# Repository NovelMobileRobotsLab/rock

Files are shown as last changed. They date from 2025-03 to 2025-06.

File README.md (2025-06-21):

# Rolling One-motor Controlled rocK (ROCK)

<p float="middle">
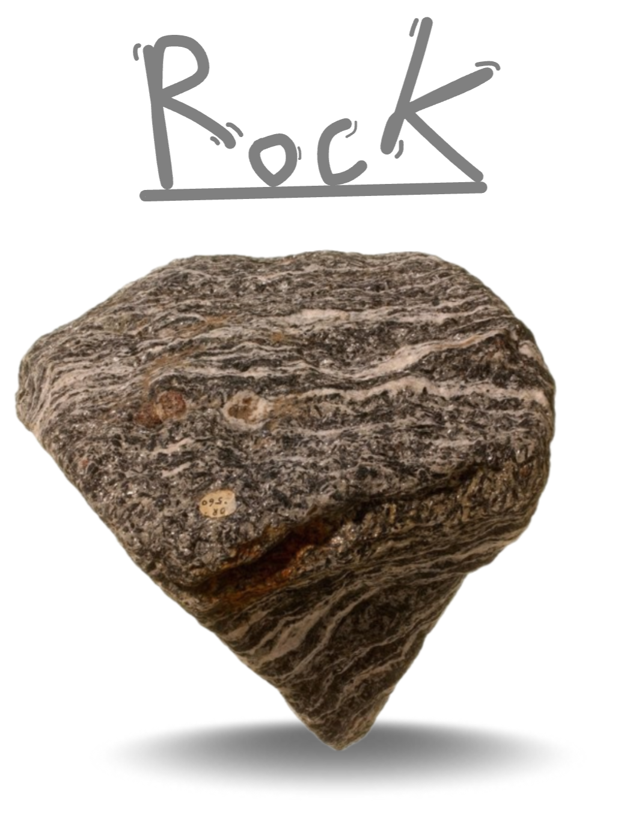
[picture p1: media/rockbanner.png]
  
</p>

A fully enclosed shape that tumbles and jumps; controllable movement on a flat surface with only 1 motor and 2 rigid bodies.

<p float="middle">
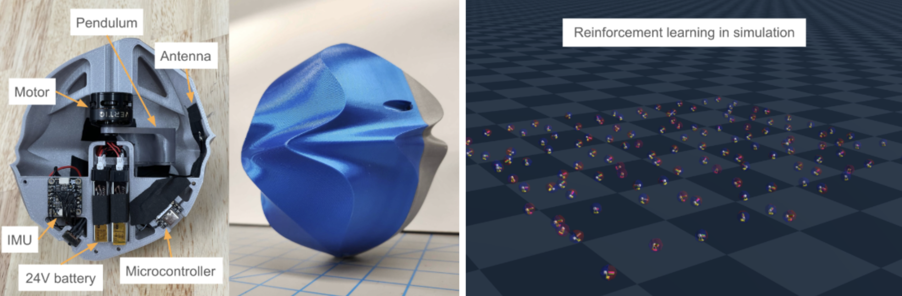
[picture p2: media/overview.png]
  
</p>

<p float="middle">
  
</p>

# Hardware
- Microcontroller: Seeeduino Xiao ESP32S3
- Motor: Vertiq 23-06 G1 220KV brushless motor
- IMU: Adafruit BNO085
- Shell: 3D printed
- Pendulum: 3D printed, filled with lead
- Battery: 6x Tattu 220mAh LiPo (22.2V)

An uneven shell creates steering affordances, using the complex ground contacts to couple the dynamics between motion in multiple dimensions. We iterated over 3 designs to improve continuous rolling, consistent turning, and option for interchangable attachments for diverse maneuvers:
<p float="middle">
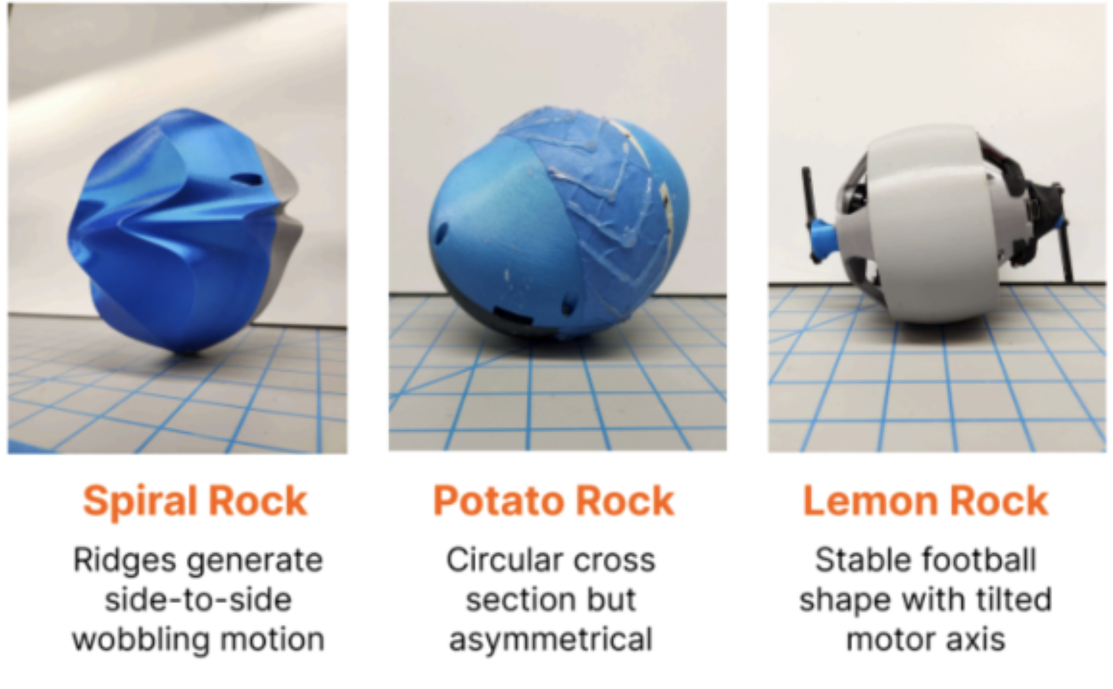
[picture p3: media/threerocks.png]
  
</p>

# Control

<p float="middle">
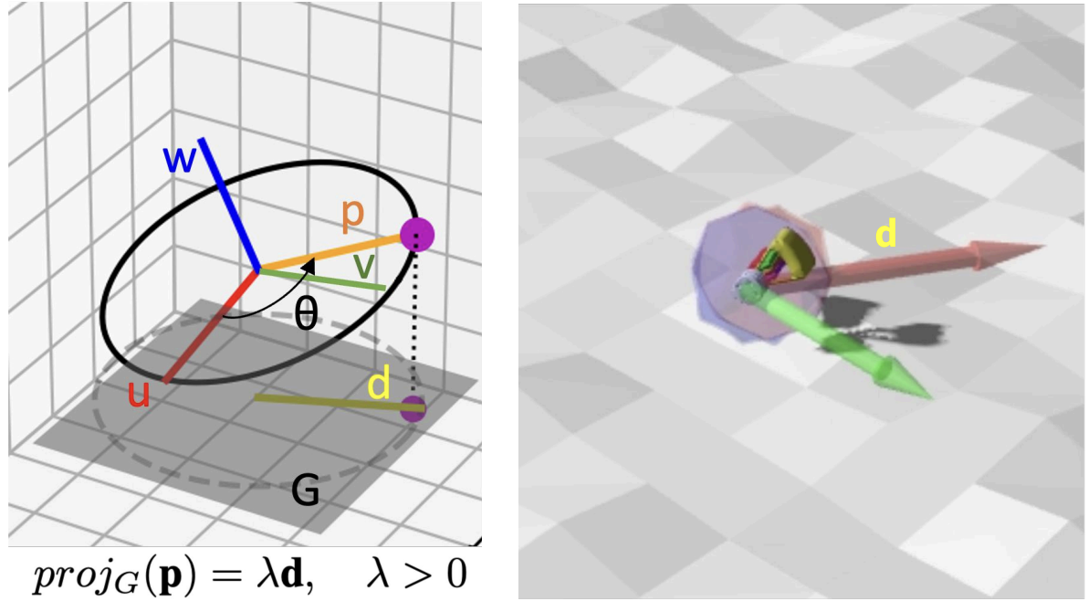
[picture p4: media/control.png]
  
</p>
The robot is teleoperated by commanding a desired rolling direction. We create a simple controller that rolls by offsetting the robot’s center of mass in the direction by manual joystick input.  We also train a reinforcement learning policy to use dynamic pendulum movements for higher performance. The policy is quantized to run on the microcontroller at 90 Hz.

<p float="middle">
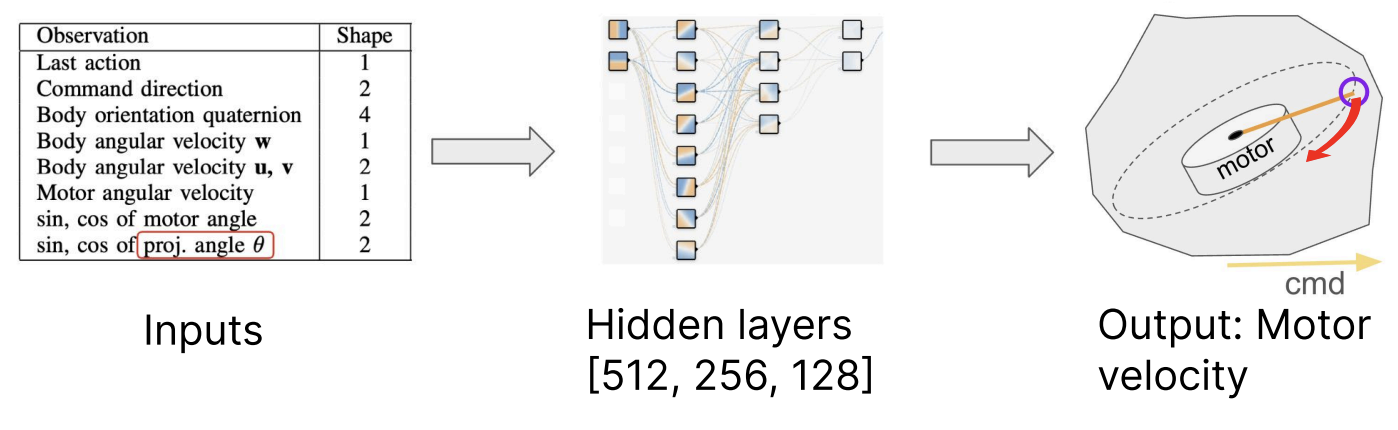
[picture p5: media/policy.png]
  
</p>

# Installation

Create python virtual environment (we use python3.12):
```bash
python3 -m venv .venv
source .venv/bin/activate
```

Install dependencies (genesis-world enforces stricter than necessary version requirements so we install it with --no-deps):
```bash
pip install -r requirements.txt
pip install genesis-world --no-deps
```

# Files directory
```
rock/
├── embedded/
│   ├── convert_torch_to_tflite/     # Convert PyTorch models to TFLite for ESP32
│   ├── esp-tf_speedtest_fw/         # PlatformIO project testing inference speed
│   ├── gimbal_prototype_fw/         # PlatformIO project gimbal prototype
│   └── rock2_fw/                    # PlatformIO project for latest ROCK
│       ├── src/                     # Source code directory
│       │   ├── main.cpp             # Main control loop firmware
│       │   ├── util.h               # Utility functions for IMU and motor control
│       │   ├── all_ops_resolver.h   # TFLite operation definitions
│       │   ├── model_13_26_700.h    # Header for trained model on rough terrain
│       │   ├── model_13_26_700.cpp  # Trained model weights on rough terrain
│       │   ├── model_58_02_200.h    # Header for trained model on smooth terrain
│       │   └── model_58_02_200.cpp  # Trained model weights on smooth terrain
│       ├── trained_models/          # Original TFLite model files
│       └── platformio.ini           # Project configuration and dependencies
├── genesis-sim/
│   ├── balancing/                   # RL environment for balancing, unfinished
│   └── tumbling/                    # RL environment for tumbling, main work
│       ├── rock_env.py              # Defines how the simulation behaves
│       ├── rock_train.py            # Start parallel simulation training
│       ├── rock_eval.py             # Run simulation for policy evaluation 
│       ├── viewer.py                # Run simulation just for viewing
│       ├── analyze_runs.ipynb       # Analyzing run performance with plots
│       ├── runs/                    # Training run output
│       ├── autoruns/                # Automated run output
│       ├── projruns/                # Runs with projection controller
│       └── penaltysweep/            # Runs with sweep of penalty weights
├── onshape/                         # updating cad in python and generating URDF
│   ├── balo/                        # almost symmetric balo shape
│   ├── balo2/                       # test hexagonal shape with stretched vertex
│   ├── intuition2/                  # spiral shell (mostly used this)
│   ├── pmrock/                      # parametric minimal rock
│   ├── rock1/                       # jointed 1 dof rock
│   └── weird_rock/                  # potato shell
├── rockstation/
│   ├── cmdlogs/                     # CSV logs from rockstation
│   ├── decode.ipynb                 # Testing telemetry decoding
│   ├── loganalysis.ipynb            # Notebook for analyzing cmdlogs
|   ├── periodics.py                 # Helper for running functions at fixed rate
│   └── rockstation1-5.py            # Run this to control the robot from laptop
└── sandbox/
    ├── acrobot/                     # Jumping rock is kinda like acrobot
    ├── from_matlab/                 # Prof Yim's MATLAB dynamics, translated
    ├── gpu_accel/                   # Messing around with Taichi and trajopt
    ├── imu_sim/                     # Attempt at velocity estimator from IMU
    ├── littlewood_hoop/             # Unbalanced hoop that jumps
    ├── model_tumbling/              # Projection controller interactive
    ├── quaternions/                 # Visualizing quaternions for IMU calcs
    ├── trajopt/                     # Casadi trajopt
    └── util/                        # Plotting utilities
```

## Most useful files

### `embedded/rock2_fw/src/main.cpp`
Platformio project to control the current prototype that consists of a heavy lead pendulum spinning inside a shell (only 2 rigid bodies). 
- TFLite model inference on ESP32S3 for control
- BNO085 IMU integration for orientation sensing
- Vertiq motor control with configurable parameters
- ESP-NOW wireless communication for remote control
- Support for multiple rock designs (spiral, potato, faceless) with different motor/IMU configurations
- Real-time control loop running at 200Hz with IMU-based feedback

### `embedded/rock2_fw/trained_models/to_tflite.ipynb`
Python notebook to convert a trained pytorch model into a .cpp and .h file that can be copied into an firmware project. Load the model using the ESP-TF Arduino library to perform inference on the ESP32S3. Will quantize the model using int8 in order to use optimized matrix operations using ESP-NN specific to the ESP32S3.

### `embedded/esp-tf_speedtest_fw/`
Platformio project to test inference speed of a fully connected neural network using the ESP-TF Arduino library. The model is trained and converted using the jupyter notebooks in `convert_torch_to_tflite`, which generates the .cpp and .h file. Uses the Seeeduino XIAO ESP32S3 and requires no hardware connections.

### `onshape/intuition2/get_urdf.py`
Each subdirectory in onshape/ corresponds to a different prototype and contains the URDF file, meshes, and script to generate the URDF. get_urdf.py is a script to modify Onshape variables and generate the URDF. Use the URDF Visualizer VS Code extension to visualize the URDF.

### `genesis-sim/tumbling/rock_env.py`
The simulation environment for the ROCK project using the Genesis physics engine. Here the terrain, simulation step, observations, actions, and reward functions are defined. 

### `rockstation/rockstation4.py`
Control station software for interfacing with the physical ROCK prototypes through the e-stop (see https://github.com/novelMobileRobotsLab/pinto-squirrel for estop setup). Includes serial communication, joystick control, and telemetry handling. The `cmdlogs` directory contains logs of commands sent to the rock.

## Operation

Very similar to the [Pinto Squirrel](https://github.com/novelMobileRobotsLab/pinto-squirrel). 

1. **Connect Estop to Laptop**
   - Connect estop device to laptop via USB
   - Determine COM port (Windows) or serial port (Linux/Mac)
   - Update the `port` variable in `rockstation4.py`
   - Verify small yellow light near USB port is blinking on estop

2. **Run Station Software**
   - Execute `python rockstation4.py`
   - Should display: "estop_ok" and "gamepad disconnected"

3. **Connect Gamepad**
   - Connect BINBOK Nintendo Switch controller (or Xbox controller) via Bluetooth or USB
   - Use apps like joystickMonitor to verify laptop can read controller
   - Terminal should display: "please calibrate joysticks"
   - Calibrate joysticks by moving them in a circle around the boundary

4. **Power On Robot**
   - Connect 6S LiPo battery (voltage must be >20V) and flip switch
   - Vertiq motors make a sound

5. **Release Emergency Stop**
   - Twist to unpress the estop button if pressed

6. **Joystick Control**
   - Hold the right bumper (index finger) to enable joystick control
   - Right joystick controls the robot rolling direction (spiral rock or potato rock) or pendulum angle with respect to gravity (lemon/faceless rock)
   - Left joystick controls the raw pendulum voltage (can spin very fast!)
   - Holding right trigger (middle finger) will enable neural net control using right joystick

7. **Telemetry**
   - The terminal will display the robot's telemetry like battery voltage, motor speed, and IMU orientation
   - The telemetry can be logged to `cmdlogs/` if csv writing lines are uncommented in `rockstation4.py`

<p float="middle">
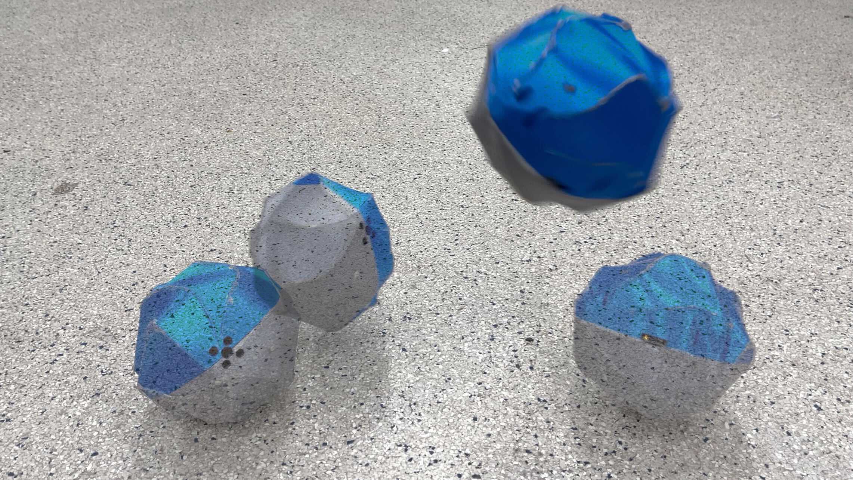
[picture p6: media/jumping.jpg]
  
</p>

## Other links
- Box: https://uofi.box.com/s/ce05dxp6a3c5nzs4ssj1djv3fu2zbas0 
- Offboarding Doc (summary): https://uofi.box.com/s/l9rvpnbomtzitpidy1dohexe3kvcctp4 
- Miro: https://miro.com/app/board/uXjVLCX5D08=/?share_link_id=853017013042
- Workshop abstract: https://arxiv.org/abs/2504.11748

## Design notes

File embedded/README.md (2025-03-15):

# Embedded firmware for ROCK

## `convert_torch_to_tflite`
Python notebooks to convert a trained pytorch model into a .cpp and .h file that can be copied into an firmware project. Load the model using the ESP-TF Arduino library to perform inference on the ESP32S3. Will quantize the model using int8 in order to use optimized matrix operations using ESP-NN specific to the ESP32S3. 

## `gimbal_prototype_fw` 
Platformio project to control the "rock1", the first prototype that consists of a slightly slanted unbalanced flywheel that freely rotates on a vertically aligned gimbal. Uses the Seeeduino XIAO ESP32S3 and Vertiq 23-06 220KV brushless motor module.

## `esp-tf_speedtest_fw`
Platformio project to test inference speed of a fully connected neural network using the ESP-TF Arduino library. The model is trained and converted using the jupyter notebooks in `convert_torch_to_tflite`, which generates the .cpp and .h file. Uses the Seeeduino XIAO ESP32S3 and requires no hardware connections.

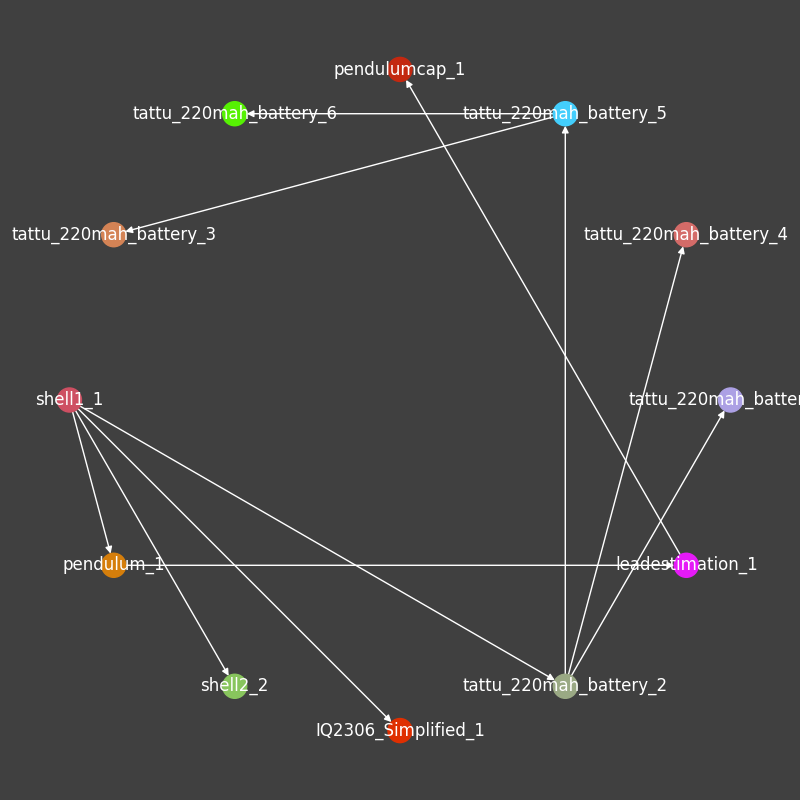
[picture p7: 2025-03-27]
onshape/weird_rock/hellorock_elec.png

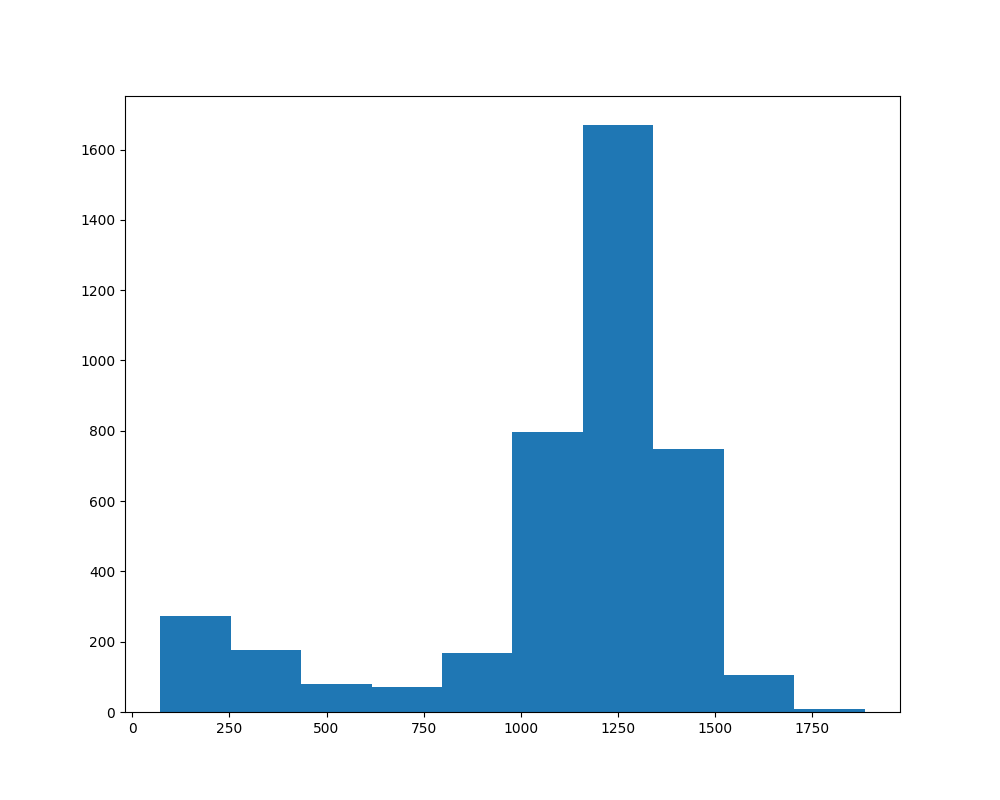
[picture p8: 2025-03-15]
sandbox/trajopt/losses/loss_all12.png

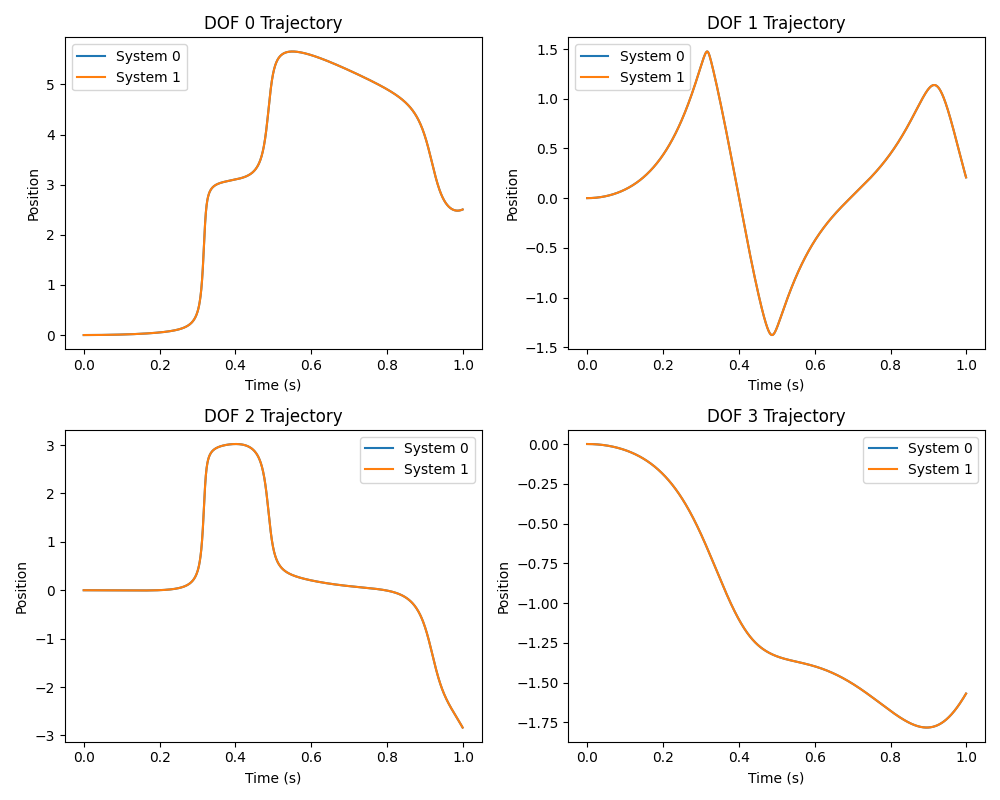
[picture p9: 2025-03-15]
sandbox/trajopt/dynamics_simple.png

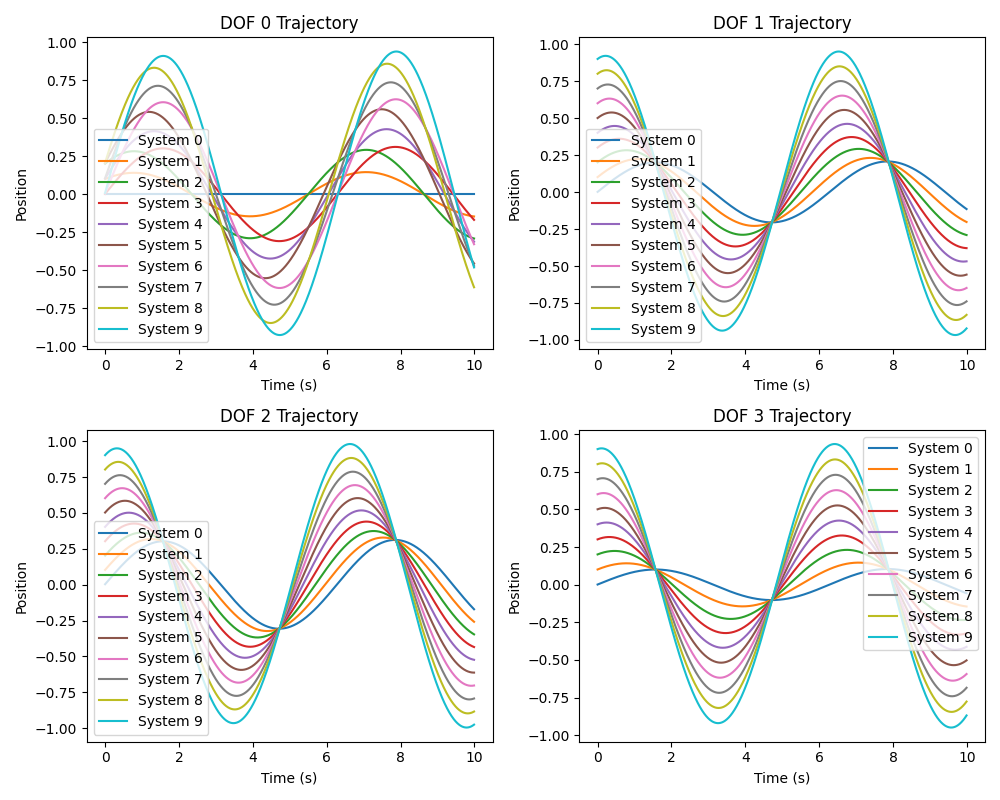
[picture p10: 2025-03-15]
sandbox/gpu_accel/trajectory2.png

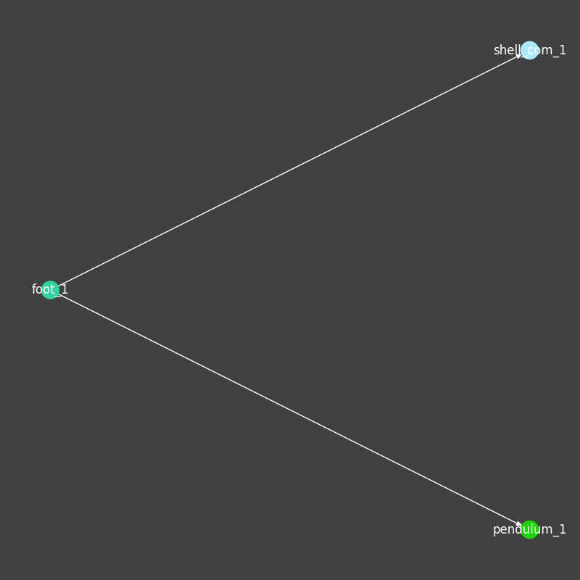
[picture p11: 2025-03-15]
onshape/pmrock/pmrock.png

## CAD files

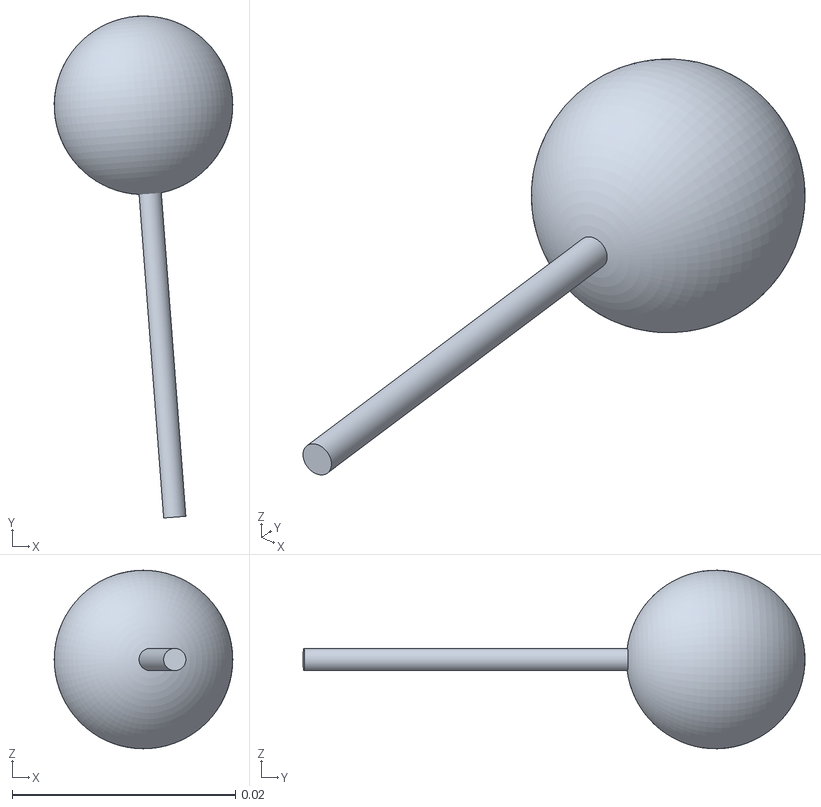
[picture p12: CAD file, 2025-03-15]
onshape/balo/meshes/pendulum_1.stl
0.016 x 0.045 x 0.016

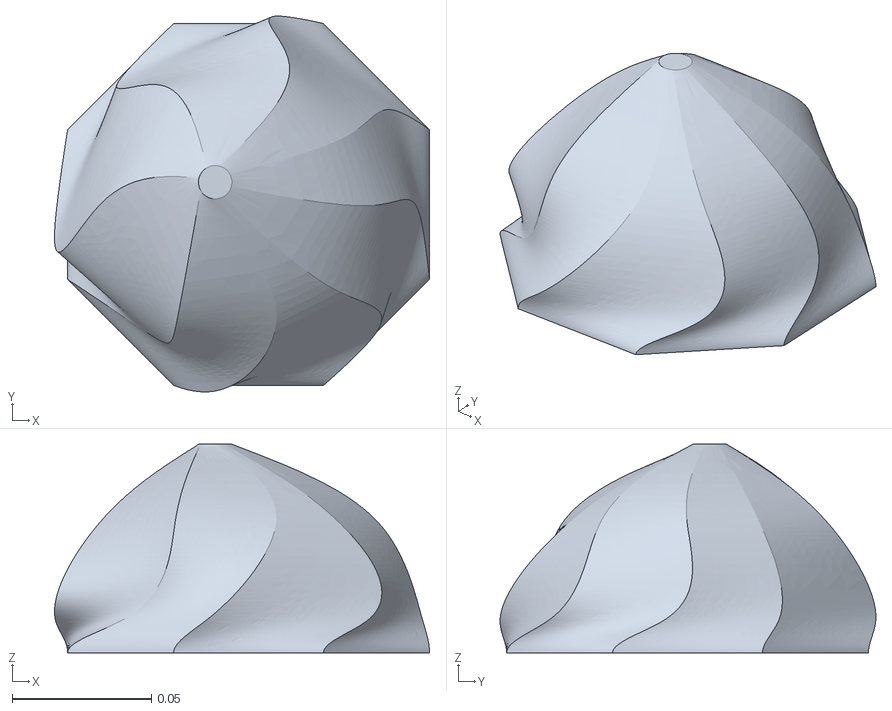
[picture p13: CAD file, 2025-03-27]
onshape/intuition2/meshes/shell2_1.stl
0.135 x 0.135 x 0.075

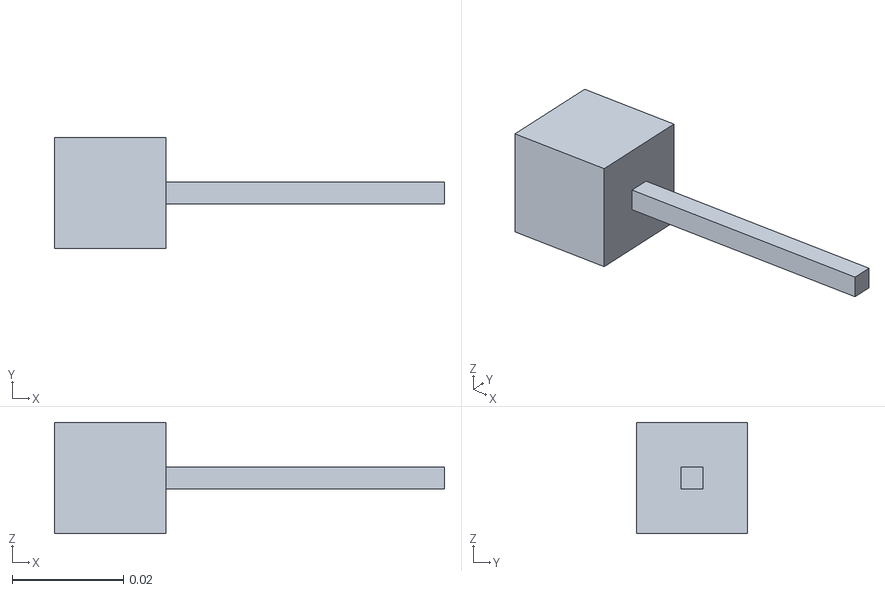
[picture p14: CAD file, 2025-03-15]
onshape/pmrock/meshes/pendulum_1.stl
0.07 x 0.02 x 0.02

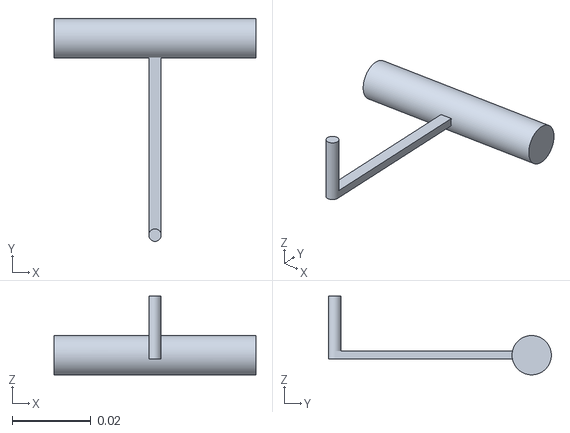
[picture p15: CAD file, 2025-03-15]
onshape/rock1/meshes/hammer_1.stl
0.0513 x 0.0566 x 0.02

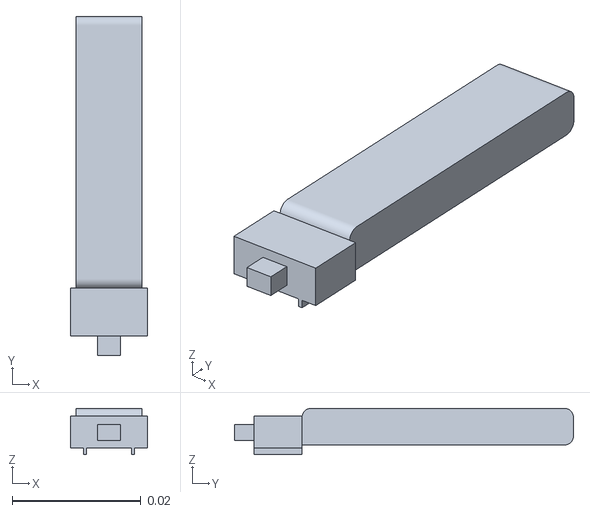
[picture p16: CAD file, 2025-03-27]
onshape/weird_rock/meshes/tattu_220mah_battery_3.stl
0.012 x 0.0527 x 0.0072

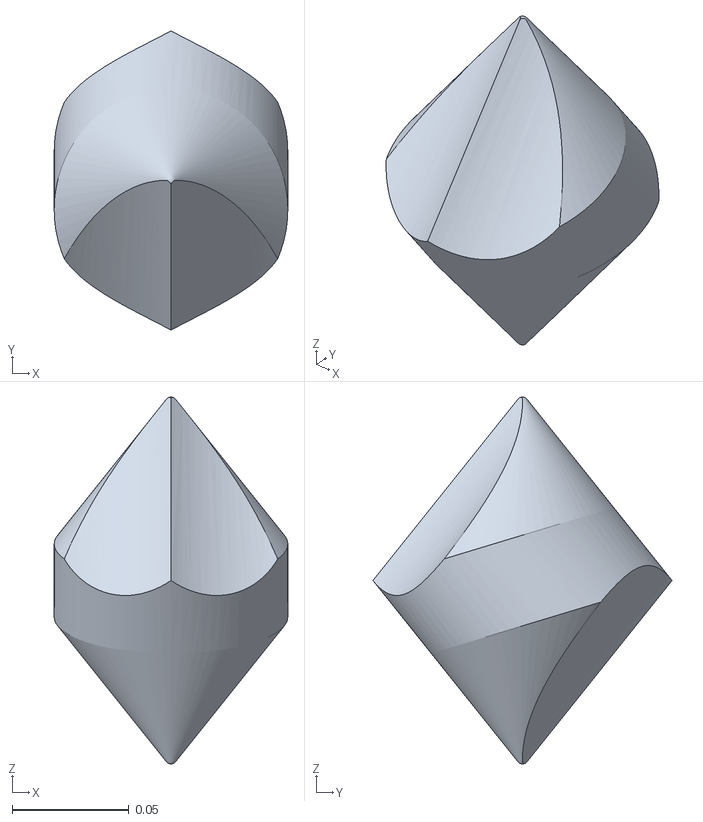
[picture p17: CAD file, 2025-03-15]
onshape/balo/meshes/shell_1.stl
0.1 x 0.128 x 0.157

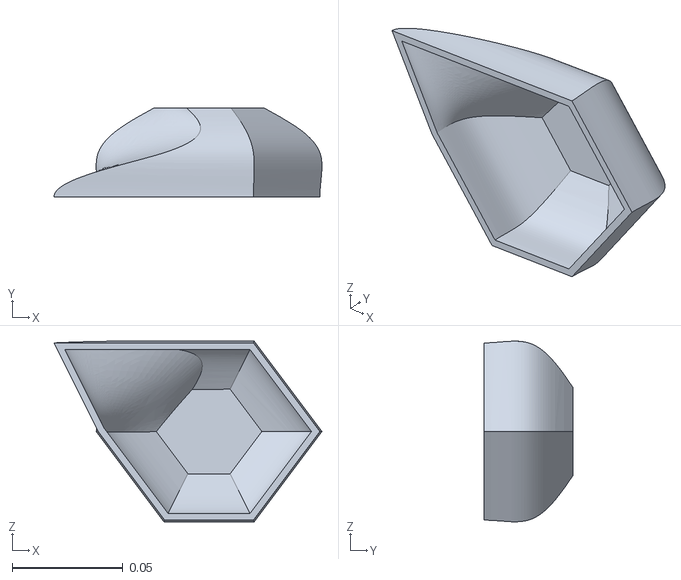
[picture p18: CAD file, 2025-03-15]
onshape/balo2/meshes/shell1_1.stl
0.121 x 0.04 x 0.0816

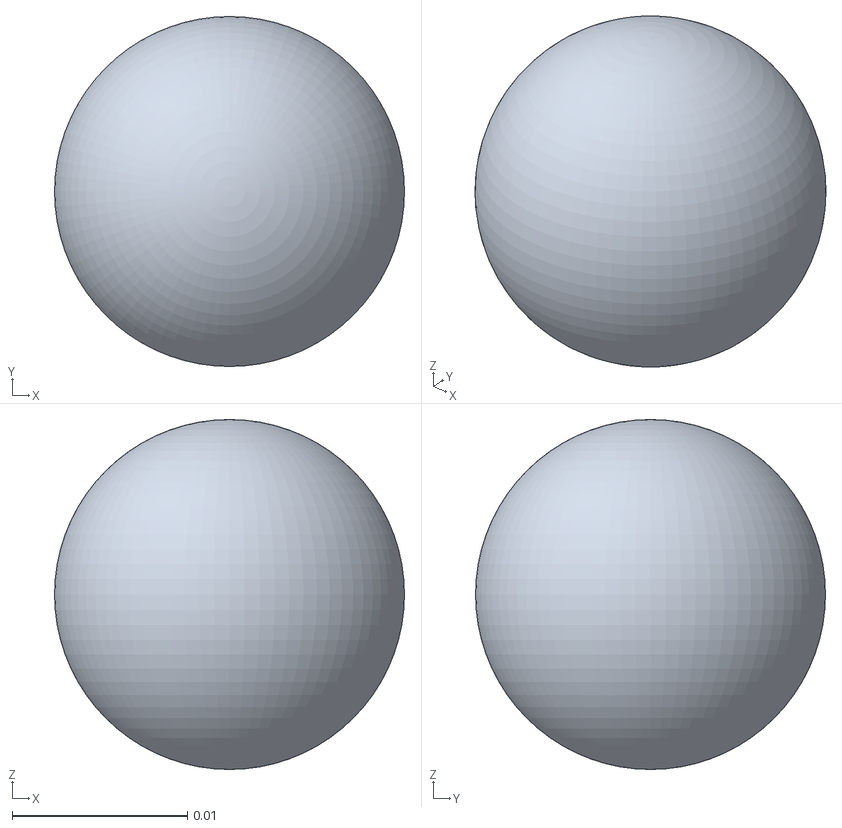
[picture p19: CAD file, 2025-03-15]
onshape/pmrock/meshes/foot_1.stl
0.02 x 0.02 x 0.02

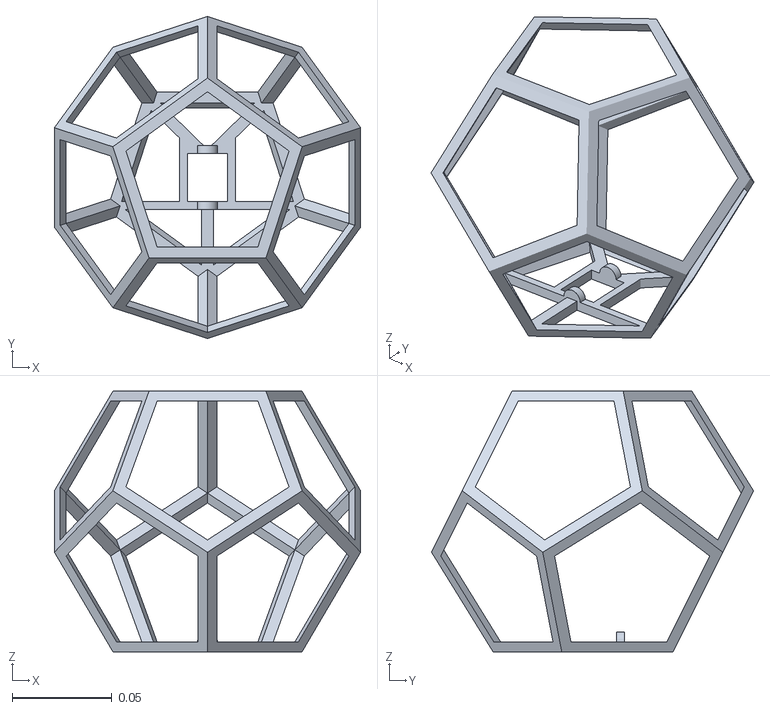
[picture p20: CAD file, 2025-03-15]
onshape/rock1/meshes/root_1.stl
0.154 x 0.162 x 0.131

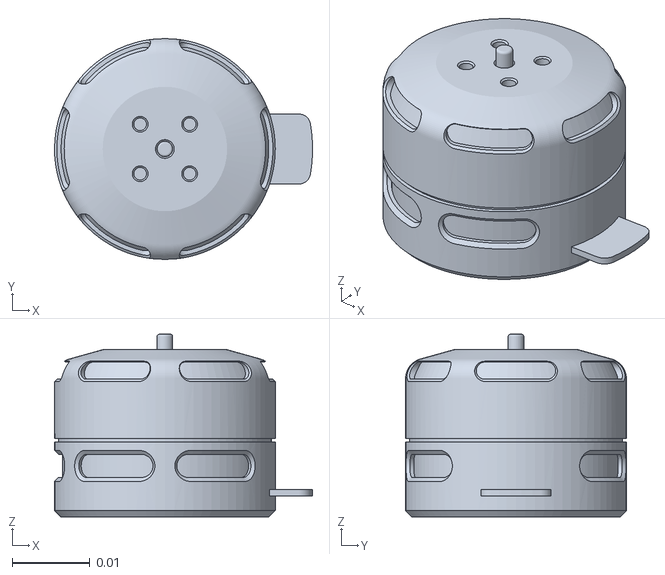
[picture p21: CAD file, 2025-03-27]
onshape/weird_rock/meshes/IQ2306_Simplified_1.stl
0.0332 x 0.0284 x 0.0235

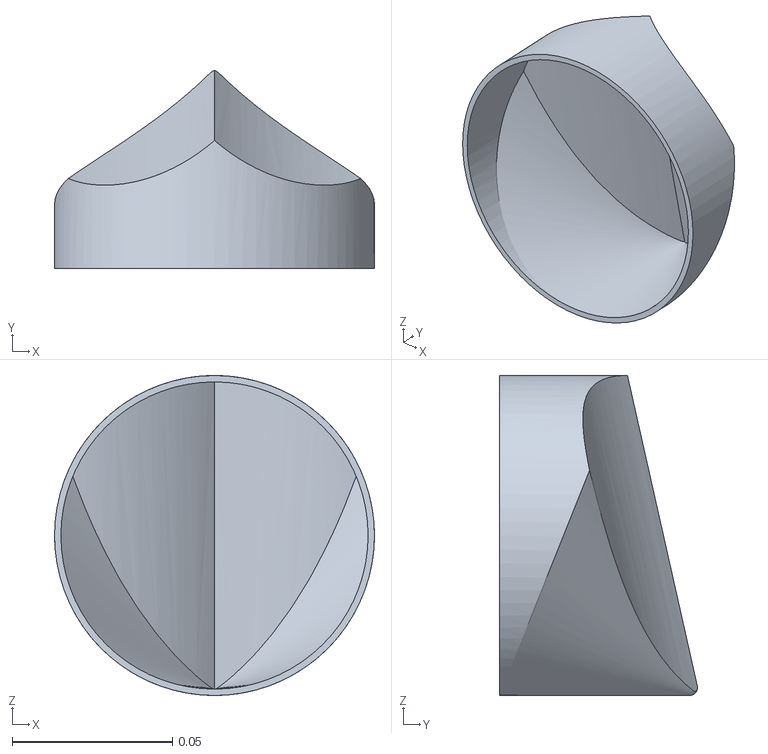
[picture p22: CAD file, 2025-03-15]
onshape/balo/meshes/bottomshell_1.stl
0.1 x 0.0619 x 0.1

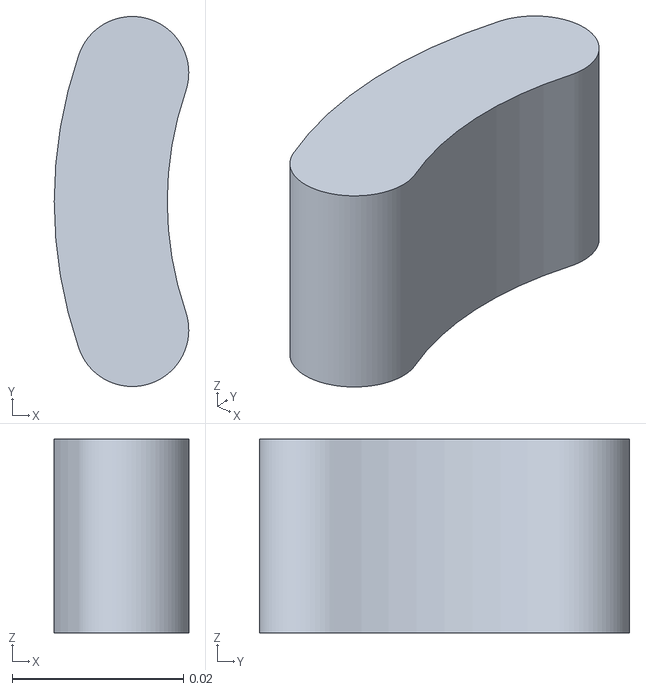
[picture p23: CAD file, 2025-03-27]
onshape/intuition2/meshes/leadestimation_1.stl
0.0157 x 0.0432 x 0.0226

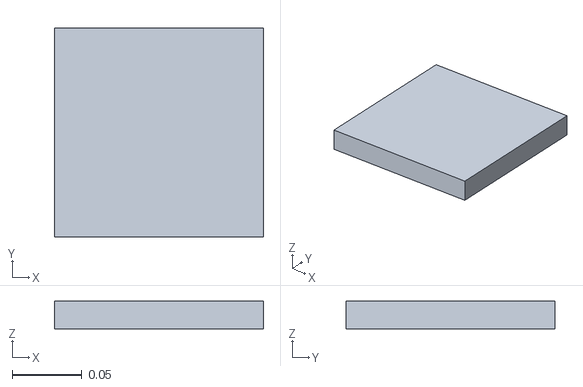
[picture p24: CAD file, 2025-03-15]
onshape/pmrock/meshes/shell_com_1.stl
0.15 x 0.15 x 0.02

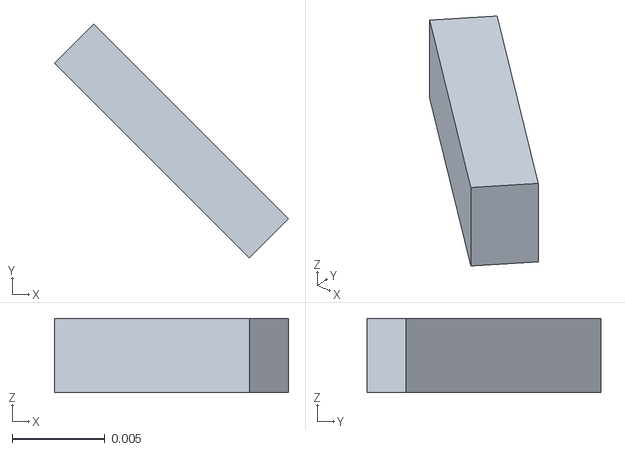
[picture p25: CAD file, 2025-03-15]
onshape/rock1/meshes/Part_2_1.stl
0.0126 x 0.0126 x 0.004

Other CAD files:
onshape/intuition2/meshes/2x3_battery_pack_1_SUB_tattu_220mah_battery_4.stl
onshape/weird_rock/meshes/Part_1_2.stl
onshape/balo/meshes/topshell_1.stl
onshape/intuition2/meshes/pendulumcap_1.stl
onshape/balo2/meshes/pendulum_1.stl
onshape/balo2/meshes/shell2_1.stl
onshape/intuition2/meshes/2x3_battery_pack_1_SUB_tattu_220mah_battery_1.stl
onshape/intuition2/meshes/2x3_battery_pack_1_SUB_tattu_220mah_battery_2.stl
onshape/intuition2/meshes/2x3_battery_pack_1_SUB_tattu_220mah_battery_3.stl
onshape/intuition2/meshes/2x3_battery_pack_1_SUB_tattu_220mah_battery_5.stl
onshape/intuition2/meshes/2x3_battery_pack_1_SUB_tattu_220mah_battery_6.stl
onshape/intuition2/meshes/IQ2306_Simplified_1.stl
onshape/intuition2/meshes/pendulum_1.stl
onshape/intuition2/meshes/shell_1.stl
onshape/rock1/meshes/Part_3_1.stl
onshape/rock1/meshes/Part_4_1.stl
onshape/rock1/meshes/foot_1.stl
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

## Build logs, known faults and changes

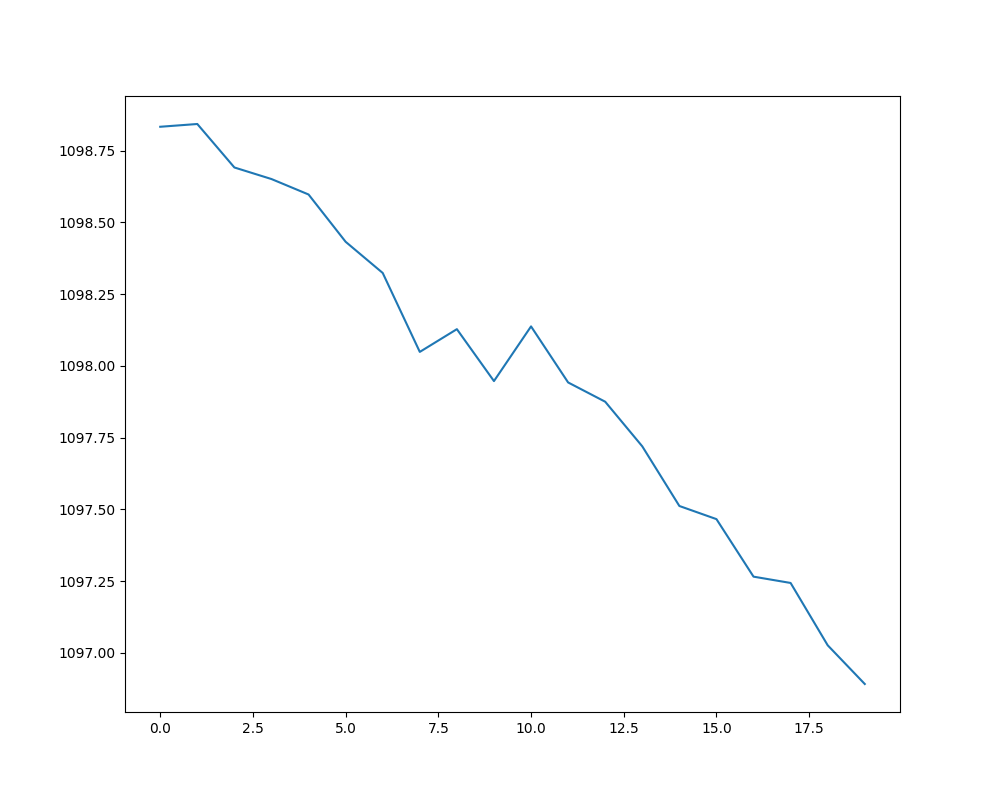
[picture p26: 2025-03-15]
sandbox/trajopt/losses/loss_history2.png

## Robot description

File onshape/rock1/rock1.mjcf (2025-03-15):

<robot name="test">
  <link name="root_1">
    <visual name="root_1_visual">
      <origin xyz="0 0 0" rpy="0 0 0"/>
      <geometry>
        <mesh filename="meshes/root_1.stl"/>
      </geometry>
      <material name="root_1-material">
        <color rgba="0 0 1 1"/>
      </material>
    </visual>
    <collision name="root_1_collision">
      <origin xyz="0 0 0" rpy="0 0 0"/>
      <geometry>
        <mesh filename="meshes/root_1.stl"/>
      </geometry>
    </collision>
    <inertial>
      <mass value="0.14070459"/>
      <inertia ixx="0.00053886708" iyy="0.00053657154" izz="0.00048673883" ixy="0" ixz="0" iyz="2.5574782e-07"/>
      <origin xyz="0 0 0" rpy="0 0 0"/>
    </inertial>
  </link>
  <link name="mount_1">
    <visual name="mount_1_visual">
      <origin xyz="0 0 0" rpy="0 0 0"/>
      <geometry>
        <mesh filename="meshes/mount_1.stl"/>
      </geometry>
      <material name="mount_1-material">
        <color rgba="1 0 0 1"/>
      </material>
    </visual>
    <collision name="mount_1_collision">
      <origin xyz="0 0 0" rpy="0 0 0"/>
      <geometry>
        <mesh filename="meshes/mount_1.stl"/>
      </geometry>
    </collision>
    <inertial>
      <mass value="0.037144641"/>
      <inertia ixx="1.7960371e-05" iyy="2.1752436e-06" izz="1.7723066e-05" ixy="2.485767e-06" ixz="0" iyz="0"/>
      <origin xyz="-0.002836331 0.036726416 -0.01" rpy="0 0 0"/>
    </inertial>
  </link>
  <link name="hammer_1">
    <visual name="hammer_1_visual">
      <origin xyz="0 0 0" rpy="0 0 0"/>
      <geometry>
        <mesh filename="meshes/hammer_1.stl"/>
      </geometry>
      <material name="hammer_1-material">
        <color rgba="0 0 0 1"/>
      </material>
    </visual>
    <collision name="hammer_1_collision">
      <origin xyz="0 0 0" rpy="0 0 0"/>
      <geometry>
        <mesh filename="meshes/hammer_1.stl"/>
      </geometry>
    </collision>
    <inertial>
      <mass value="0.012062541"/>
      <inertia ixx="1.57236e-06" iyy="2.4984784e-06" izz="3.885809e-06" ixy="0" ixz="0" iyz="1.1308963e-07"/>
      <origin xyz="8.2580513e-23 0.046887655 -0.014800048" rpy="0 0 0"/>
    </inertial>
  </link>
  <joint name="Revolute_2" type="revolute">
    <origin xyz="2.1906919e-16 -0.010032667 -0.053219852" rpy="1.5707963 0 -9.9920072e-16"/>
    <parent link="root_1"/>
    <child link="mount_1"/>
    <axis xyz="0 0 -1"/>
    <limit effort="1" velocity="1" lower="-6.2831853" upper="6.2831853"/>
  </joint>
  <joint name="Revolute_1" type="revolute">
    <origin xyz="-0.005 0.06045085 -0.01" rpy="-3.1415927 1.5707963 0"/>
    <parent link="mount_1"/>
    <child link="hammer_1"/>
    <axis xyz="0 0 -1"/>
    <limit effort="1" velocity="1" lower="-6.2831853" upper="6.2831853"/>
  </joint>
</robot>

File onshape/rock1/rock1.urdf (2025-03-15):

<?xml version="1.0" ?>
<robot name="test">
  <link name="foot_1">
    <visual name="foot_1_visual">
      <origin xyz="0 0 0" rpy="0 0 0"/>
      <geometry>
        <mesh filename="meshes/foot_1.stl"/>
      </geometry>
      <material name="foot_1-material">
        <color rgba="0 1 1 1"/>
      </material>
    </visual>
    <collision name="foot_1_collision">
      <origin xyz="0 0 0" rpy="0 0 0"/>
      <geometry>
        <mesh filename="meshes/foot_1.stl"/>
      </geometry>
    </collision>
    <inertial>
      <mass value="0"/>
      <inertia ixx="0" iyy="0" izz="0" ixy="0" ixz="0" iyz="0"/>
      <origin xyz="0 0 0" rpy="0 0 0"/>
    </inertial>
  </link>
  <link name="Part_2_1">
    <visual name="Part_2_1_visual">
      <origin xyz="0 0 0" rpy="0 0 0"/>
      <geometry>
        <mesh filename="meshes/Part_2_1.stl"/>
      </geometry>
      <material name="Part_2_1-material">
        <color rgba="0 1 0 1"/>
      </material>
    </visual>
    <collision name="Part_2_1_collision">
      <origin xyz="0 0 0" rpy="0 0 0"/>
      <geometry>
        <mesh filename="meshes/Part_2_1.stl"/>
      </geometry>
    </collision>
    <inertial>
      <mass value="0"/>
      <inertia ixx="0" iyy="0" izz="0" ixy="0" ixz="0" iyz="0"/>
      <origin xyz="-4.1359031e-19 0.0015 -2.7572687e-19" rpy="0 0 0"/>
    </inertial>
  </link>
  <link name="Part_3_1">
    <visual name="Part_3_1_visual">
      <origin xyz="0 0 0" rpy="0 0 0"/>
      <geometry>
        <mesh filename="meshes/Part_3_1.stl"/>
      </geometry>
      <material name="Part_3_1-material">
        <color rgba="1 1 1 1"/>
      </material>
    </visual>
    <collision name="Part_3_1_collision">
      <origin xyz="0 0 0" rpy="0 0 0"/>
      <geometry>
        <mesh filename="meshes/Part_3_1.stl"/>
      </geometry>
    </collision>
    <inertial>
      <mass value="0"/>
      <inertia ixx="0" iyy="0" izz="0" ixy="0" ixz="0" iyz="0"/>
      <origin xyz="-0.015948197 0 0.014494675" rpy="0 0 0"/>
    </inertial>
  </link>
  <link name="Part_4_1">
    <visual name="Part_4_1_visual">
      <origin xyz="0 0 0" rpy="0 0 0"/>
      <geometry>
        <mesh filename="meshes/Part_4_1.stl"/>
      </geometry>
      <material name="Part_4_1-material">
        <color rgba="1 1 1 1"/>
      </material>
    </visual>
    <collision name="Part_4_1_collision">
      <origin xyz="0 0 0" rpy="0 0 0"/>
      <geometry>
        <mesh filename="meshes/Part_4_1.stl"/>
      </geometry>
    </collision>
    <inertial>
      <mass value="0"/>
      <inertia ixx="0" iyy="0" izz="0" ixy="0" ixz="0" iyz="0"/>
      <origin xyz="-0.014948197 0 0.016494675" rpy="0 0 0"/>
    </inertial>
  </link>
  <joint name="Revolute_1" type="revolute">
    <origin xyz="-2.1684043e-19 0 0.0015" rpy="-1.5707963 0 0"/>
    <parent link="foot_1"/>
    <child link="Part_2_1"/>
    <axis xyz="0 0 -1"/>
    <limit effort="1" velocity="1" lower="-6.2831853" upper="6.2831853"/>
  </joint>
  <joint name="Slider_1" type="prismatic">
    <origin xyz="0.0094664182 -0.011587739 -2.7572687e-19" rpy="-1.5707963 0 -0.78539816"/>
    <parent link="Part_2_1"/>
    <child link="Part_3_1"/>
    <axis xyz="0 0 -1"/>
    <limit effort="1" velocity="1" lower="-0.1" upper="0.1"/>
  </joint>
  <joint name="Revolute_2" type="revolute">
    <origin xyz="-0.001 -4.1359031e-19 -0.002" rpy="0 0 0"/>
    <parent link="Part_3_1"/>
    <child link="Part_4_1"/>
    <axis xyz="0 0 -1"/>
    <limit effort="1" velocity="1" lower="-6.2831853" upper="6.2831853"/>
  </joint>
</robot>

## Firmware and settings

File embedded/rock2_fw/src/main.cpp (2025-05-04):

#include <Arduino.h>
#include <Adafruit_BNO08x.h>
#include <iq_module_communication.hpp>
#include <esp_now.h>
#include <WiFi.h>

#include <model_58_02_200.h>
#include <model_13_26_700.h>

#include <vector>
#include <base64.hpp>

#include <all_ops_resolver.h>
#include "tensorflow/lite/micro/tflite_bridge/micro_error_reporter.h"
#include "tensorflow/lite/micro/micro_interpreter.h"
#include "tensorflow/lite/schema/schema_generated.h"

#include "util.h"

#define TAG "main"
#define INPUT_SIZE 15*3
#define BNO08X_CS 6
#define BNO08X_INT 5
#define BNO08X_RESET 1

// //58_02_200
// #define input_scale 0.007843082770705223f
// #define input_zero_pt -1
// #define output_scale 0.01251873467117548f
// #define output_zero_pt -14

// 13_26_700
#define input_scale 0.00784307811409235f
#define input_zero_pt 0
#define output_scale 0.028471535071730614f
#define output_zero_pt -12

/*
    0: spiral rock
    1: potato rock
    2: faceless rock
*/
#define ROCK_ID 2


/*
motor_zero: what motor reports when pendulum is pointing in the direction of IMU position

origin vectors are the pendulum U,V,W axes in the IMU frame
U: direction pendulum is pointing at motor zero position
V: on pendulum plane, find using right hand rule
W: motor axis pointing outwards

q_imu_to_global: {x, y, z, w} static quaternion to transform sensor quat_imu to global frame
*/
#if ROCK_ID == 0 // spiral rock
    float motor_zero = -0.05235987755f; //radians
    float u_origin[3] = {0,-1,0};
    float v_origin[3] = {0,0,-1};
    float w_origin[3] = {1,0,0};
    float q_imu_to_global[4] = {0, 0.7071068, 0.7071068, 0}; //z axis inverted, x and y swap without negating
#elif ROCK_ID == 1 // potato rock
    float motor_zero = -0.628319; //radians
    float u_origin[3] = {-1,0,0}; 
    float v_origin[3] = {0,0,-1}; 
    float w_origin[3] = {0,-1,0}; 
    float q_imu_to_global[4] = {0, 0.7071068, -0.7071068, 0}; //untested
#elif ROCK_ID == 2 // faceless rock
    float motor_zero = -2.0769418; //radians
    float u_origin[3] = {0,1,0}; 
    float v_origin[3] = {-1,0,0}; 
    float w_origin[3] = {0,0,1}; 
    float q_imu_to_global[4] = {0, 0.7071068, -0.7071068, 0}; //untested
#endif


Adafruit_BNO08x bno08x(BNO08X_RESET);
sh2_SensorValue_t sensorValue;
sh2_SensorId_t reportType = SH2_ARVR_STABILIZED_RV;
// sh2_SensorId_t reportType = SH2_GYRO_INTEGRATED_RV; //faster?

long reportIntervalUs = 5000;
void setReports(sh2_SensorId_t reportType, long report_interval) {
    Serial.println("Setting desired reports");
    if (!bno08x.enableReport(reportType, report_interval)) {
        Serial.println("Could not enable stabilized remote vector");
    }
}

IqSerial ser(Serial1);
PowerMonitorClient power(0);
MultiTurnAngleControlClient angle(0);
CoilTemperatureEstimatorClient coil(0);

uint8_t estop_mac_addr[] = {0x30, 0x30, 0xF9, 0x34, 0x52, 0xA0};


String receivedString = "";
char send_str[255];

void OnDataRecv(const uint8_t *mac, const uint8_t *incomingData, int len) { // len should not be longer than 250bytes
    receivedString = String((char *)incomingData);
}

void OnDataSent(const uint8_t *mac_addr, esp_now_send_status_t status) {

}



//tensorflow
tflite::ErrorReporter *error_reporter = nullptr;
const tflite::Model *model = nullptr;
tflite::MicroInterpreter *interpreter = nullptr;
TfLiteTensor *input = nullptr;
// An area of memory to use for input, output, and intermediate arrays.
const int kTensorArenaSize = 35 * 1024;
static uint8_t tensor_arena[kTensorArenaSize];

void printModelInfo(){
  input = interpreter->input(0);
  ESP_LOGI(TAG, "Input Shape");
  for (int i = 0; i < input->dims->size; i++)
  {
    ESP_LOGI(TAG, "%d", input->dims->data[i]);
  }

  ESP_LOGI(TAG, "Input Type: %s", TfLiteTypeGetName(input->type));
  ESP_LOGI(TAG, "Output Shape");

  TfLiteTensor *output = interpreter->output(0);
  for (int i = 0; i < output->dims->size; i++)
  {
    ESP_LOGI(TAG, "%d", output->dims->data[i]);
  }
  ESP_LOGI(TAG, "Output Type: %s", TfLiteTypeGetName(output->type));

  ESP_LOGI(TAG, "Arena Size:%d bytes of memory", interpreter->arena_used_bytes());
}




void setup() {
    delay(1000);

    setCpuFrequencyMhz(240);
    pinMode(LED_BUILTIN, OUTPUT);

    // Start Vertiq communication
    #if ROCK_ID == 0
        Serial1.begin(921600, SERIAL_8N1, D2, D3);
    #else
        Serial1.begin(115200, SERIAL_8N1, D2, D3); //old rock
    #endif

    pinMode(D1, OUTPUT);
    digitalWrite(D1, LOW); // ground reference for IQ motor
    delay(500);
    // ser.set(angle.sample_zero_angle_); //zero motor
    // ser.set(angle.obs_angular_displacement_, 0.0f); //zero motor
    
    Serial.begin(115200);

    // ESP NOW SETUP
    WiFi.mode(WIFI_MODE_STA);
    Serial.println(WiFi.macAddress());
    if (esp_now_init() != ESP_OK) {
        Serial.println("Error initializing ESP-NOW");
        delay(3000);
        ESP.restart();
    }
    esp_now_register_recv_cb(OnDataRecv);
    esp_now_register_send_cb(OnDataSent);
    esp_now_peer_info_t peerInfo = {};
    memcpy(peerInfo.peer_addr, estop_mac_addr, 6);
    peerInfo.channel = 0;
    peerInfo.encrypt = false;
    esp_now_add_peer(&peerInfo);

    // IMU init
    if (!bno08x.begin_SPI(BNO08X_CS, BNO08X_INT)) {
        Serial.println("Failed to find BNO08x chip");
        while (1) {
            delay(10);
        }
    }
    Serial.println("BNO08x Found!");
    setReports(reportType, reportIntervalUs);
    Serial.println("Reading events");


    static tflite::MicroErrorReporter micro_error_reporter;
    error_reporter = &micro_error_reporter;
    // model = tflite::GetModel(mnist_model);
    // model = tflite::GetModel(sin_model);
    // model = tflite::GetModel(sin_model_512);

    // model = tflite::GetModel(model_58_02_200);
    model = tflite::GetModel(model_13_26_700);
    if (model->version() != TFLITE_SCHEMA_VERSION){
        ESP_LOGE(TAG, "Model provided is schema version %d not equal to supported version %d.", model->version(), TFLITE_SCHEMA_VERSION);
        return;
    }
    CREATE_ALL_OPS_RESOLVER(op_resolver)

    static tflite::MicroInterpreter static_interpreter(model, op_resolver, tensor_arena, kTensorArenaSize);
    interpreter = &static_interpreter;

    // Allocate memory from the tensor_arena for the model's tensors.
    TfLiteStatus allocate_status = interpreter->AllocateTensors();
    if (allocate_status != kTfLiteOk){
        ESP_LOGE(TAG, "AllocateTensors() failed");
        return;
    }
    printModelInfo();

    // ser.set(angle.angle_Kp_, 5.0f);
    ser.set(angle.angle_Kp_, 10.0f);
    
    ser.set(angle.angle_Kd_, 0.15f);
    // ser.set(angle.angle_Kd_, 2.0f);


}



int cmdx = 4096;
int cmdy = 4096;
int leftx = 4096;
int lefty = 4096;
int run0 = 0;
long dt = 0;

float ctrl_volt_filt = 0;

float battery_lpf = 0.1;
float battery_filt = 0;

float obs[INPUT_SIZE] = {0};
float new_obs[16] = {0};

float action = 0;



float d[2] = {0, 1}; //desired direction initialized to forward
float quat_imu[4]; //orientation quaternion
float angvel_imu[3]; //in IMU frame
float angvel_urdf[3]; //transformed to simulation frame

float vel_volt_ctrl_filt = 0;
float vel_volt_ctrl_lpf = 0.9378f; //0.012 looptime


void loop() {
    //get dt
    static long last = 0;
    long now = micros();
    dt = now - last;
    last = now;

    //set desired direction from joystick
    float cmd_mag = sqrt(sq(mapf8192(cmdx)) + sq(mapf8192(cmdy))); //cmdx and cmdy are read from esp-now
    if(cmd_mag > 0.5){
        d[0] = mapf8192(cmdx) / cmd_mag;
        d[1] = mapf8192(cmdy) / cmd_mag;
    }

    // Read data from motor
    float mot_angle, mot_angvel, battery_voltage = 0;
    ser.get(angle.obs_angular_displacement_, mot_angle);
    mot_angle = mot_angle - motor_zero;
    ser.get(angle.obs_angular_velocity_, mot_angvel);
    ser.get(power.volts_, battery_voltage);
    battery_filt = (1-battery_lpf)*battery_filt + battery_lpf*battery_voltage;

    long time_mot_read = micros() - last;
    last = micros();

    // Read IMU
    if (bno08x.wasReset()) {
        Serial.print("sensor was reset ");
        setReports(reportType, reportIntervalUs);
    }
    if (bno08x.getSensorEvent(&sensorValue)) {
        quaternionToEulerRV(&sensorValue.un.arvrStabilizedRV, &ypr, true); //get roll pitch yaw angles
        // quaternionToEulerGI(&sensorValue.un.gyroIntegratedRV, &ypr, true); // faster (more noise?)

        quat_imu[0] = sensorValue.un.arvrStabilizedRV.real;
        quat_imu[1] = sensorValue.un.arvrStabilizedRV.i;
        quat_imu[2] = sensorValue.un.arvrStabilizedRV.j;
        quat_imu[3] = sensorValue.un.arvrStabilizedRV.k;

        angvel_imu[0] = sensorValue.un.gyroscope.x;
        angvel_imu[1] = sensorValue.un.gyroscope.y;
        angvel_imu[2] = sensorValue.un.gyroscope.z;
    }

    long time_imu_read = micros() - last;
    last = micros();

    
    //transform IMU angular velocities to URDF frame by rotating 180º about X axis then -90º about Z axis
    angvel_urdf[0] = angvel_imu[1];
    angvel_urdf[1] = angvel_imu[0];
    angvel_urdf[2] = -angvel_imu[2];    

    // transform IMU orientation quaternion to URDF frame by multiplying it by transformation quaternion
    float quat_urdf[4];
    rotateQuaternionbyQuaternion(quat_imu, q_imu_to_global, quat_urdf);

    // Compute U,V,W of pendulum in global frame by rotating by IMU quaternion
    float u[3]; //where pendulum points at motorangle=0, towards IMU
    float v[3]; //perpendicular to u, on pendulum circle plane, y-axis of URDF 
    float w[3]; //motor axis out of motor
    rotateVectorByQuaternion(&sensorValue.un.arvrStabilizedRV, u_origin, u); //writes to u
    rotateVectorByQuaternion(&sensorValue.un.arvrStabilizedRV, v_origin, v);
    rotateVectorByQuaternion(&sensorValue.un.arvrStabilizedRV, w_origin, w);

    float thetaD = mapf8192(cmdy)*PI;
    float asymmetry = mapf8192(leftx)*PI/2.0; // angle value added to thetaM


    float uxy = sqrt(u[0]*u[0] + u[1]*u[1]);
    if(v[2]> 0){
        uxy = -uxy;
    }

    float thetaM = (atan2f(u[2], uxy) - (thetaD - PI*0.5));
    thetaM += asymmetry*u[2];
    float thetaM_motor = thetaM ; //find closest rotation to proj_angle
    thetaM_motor = thetaM_motor + motor_zero + 2*PI*round((mot_angle - thetaM_motor) / (2*PI)); //find closest rotation to proj_angle

    float proj_angle = atan2f(-u[1]*d[0] + u[0]*d[1], v[1]*d[0]-v[0]*d[1]);
    if(w[2]<0){
        proj_angle += PI;
    }
    float proj_angle_to_motor = proj_angle + 2*PI*round((mot_angle - proj_angle) / (2*PI)); //find closest rotation to proj_angle


    //fill observations vector
    new_obs[0] = action; // last action

    new_obs[1] = quat_imu[0]; // quat_imu[0] orientation in URDF frame
    new_obs[2] = quat_imu[1]; // quat_imu[1]
    new_obs[3] = quat_imu[2]; // quat_imu[2]
    new_obs[4] = quat_imu[3]; // quat_imu[3]

    new_obs[5] = angvel_urdf[0]/12.0f; // x-axis of URDF, pointing towards seeeduino, away from IMU
    new_obs[6] = angvel_urdf[1]/24.0f; // y-axis of URDF, rolls on this axis usually
    new_obs[7] = angvel_urdf[2]/12.0f; // z-axis of URDF, points down from IMU perspective

    new_obs[8] = mot_angvel / 37.5f; // dofvel/50 (rad/s)
    new_obs[9] = sin(mot_angle); // sin(mot_angle)
    new_obs[10] = cos(mot_angle); // cos(mot_angle)

    new_obs[11] = d[0]; // command[0]
    new_obs[12] = d[1]; // command[1]

    new_obs[13] = sin(-proj_angle);
    new_obs[14] = cos(proj_angle);

    //shift observation history one later
    for (int i = INPUT_SIZE-1; i > 0; i--){
        obs[i] = obs[i-1];
    }
    for (int i = 0; i < INPUT_SIZE; i+=3){
        obs[i] = new_obs[i/3];
    }

    // Εvaluate neural net
    TfLiteTensor *input = interpreter->input(0);
    for (int i = 0; i < INPUT_SIZE; i++){
        // input->data.int8[i] = int8_t(constrain(round(obs[i] / input_scale + input_zero_pt), -128, 127));
        input->data.int8[i] = int8_t(round(obs[i] / input_scale + input_zero_pt));
    }
    long start = micros();
    if (interpreter->Invoke() == kTfLiteOk){
        // Serial.printf("Invoke in: %d microseconds\n", micros() - start);
    }else{
        Serial.printf("Invoke failed!\n");
        return;
    }
    int8_t output_int = interpreter->output(0)->data.int8[0];
    action = (output_int - output_zero_pt) * output_scale;
    long time_nn = micros() - last;
    last = micros();

    float mot_vel_des = constrain(action, -1.0f, 1.0f) * 21.0f;
    float vel_volt_ctrl = constrain((mot_vel_des - mot_angvel) * 2, -15.0f, 15.0f);

    vel_volt_ctrl_filt = (1-vel_volt_ctrl_lpf)*vel_volt_ctrl_filt + vel_volt_ctrl_lpf*vel_volt_ctrl;
    

    if (battery_filt > 20 && run0 > 0){
        if(run0 == 3 && cmd_mag > 0.5){                             //run neural net
            // ser.set(angle.ctrl_velocity_, mot_vel_des);
            ser.set(angle.ctrl_volts_, vel_volt_ctrl_filt);
        }else if(cmd_mag > 0.05){                                    //manual angle projection control
            
            //ser.set(angle.ctrl_angle_, proj_angle_to_motor);
            ser.set(angle.ctrl_angle_, thetaM_motor); 
            // float kp = 4.0f;
            // float v_proportional = constrain(kp*(proj_angle_to_motor - mot_angle), -12.0f, 12.0f);
            // ser.set(angle.ctrl_volts_, v_proportional);

        }else if(abs(mapf8192(lefty)) > 0.2){                       //manual voltage control
            ser.set(angle.ctrl_volts_, mapf8192(lefty) * 12.0f);
        }else{
            ser.set(angle.ctrl_volts_, 0.0f);
        }
    }else{
        ser.set(angle.ctrl_volts_, 0.0f);
    }

    long time_mot_set = micros() - last;
    last = micros();



    // ESP NOW receive and send
    if (receivedString.indexOf("cmdx") != -1) { // data exists
        cmdx = receivedString.substring(receivedString.indexOf("cmdx") + 5, receivedString.indexOf("cmdx") + 10).toInt();
        cmdy = receivedString.substring(receivedString.indexOf("cmdy") + 5, receivedString.indexOf("cmdy") + 10).toInt();
        leftx = receivedString.substring(receivedString.indexOf("leftx") + 6, receivedString.indexOf("leftx") + 11).toInt();
        lefty = receivedString.substring(receivedString.indexOf("lefty") + 6, receivedString.indexOf("lefty") + 11).toInt();
        run0 = receivedString.substring(receivedString.indexOf("run0") + 5, receivedString.indexOf("run0") + 10).toInt();
    }


    

    size_t send_str_size = sprintf(send_str,
        "v:%.2f\n"
        ,
        battery_voltage
    );
    // esp_now_send(estop_mac_addr, (uint8_t *) send_str, send_str_size);

    long time_espnow = micros() - last;

    std::vector<float> telemetry;
    telemetry.push_back(battery_filt);
    telemetry.push_back(mot_angle);
    telemetry.push_back(mot_angvel);
    telemetry.push_back(thetaM_motor); //des motor angle
    telemetry.push_back(quat_imu[0]);
    telemetry.push_back(quat_imu[1]);
    telemetry.push_back(quat_imu[2]);
    telemetry.push_back(quat_imu[3]);
    telemetry.push_back(angvel_imu[0]);
    telemetry.push_back(angvel_imu[1]);
    telemetry.push_back(angvel_imu[2]);

    size_t in_len_bytes = telemetry.size() * sizeof(float); //  How many bytes of raw float data?
    const unsigned char* in_ptr = reinterpret_cast<const unsigned char*>(telemetry.data());
    unsigned int max_out_len = static_cast<unsigned int>(((in_len_bytes + 2) / 3) * 4 + 1); //Compute a safe upper‑bound on Base64 output length
    std::unique_ptr<unsigned char[]> out_buf(new unsigned char[max_out_len]); //Allocate the output buffer
    unsigned int encoded_len = encode_base64(in_ptr, static_cast<unsigned int>(in_len_bytes), out_buf.get()); // Call encoder
    const char* payload = reinterpret_cast<const char*>(out_buf.get());
    esp_now_send(estop_mac_addr, (uint8_t *) payload, encoded_len);

    // Serial.printf("dt: %d\n", dt);
    // Serial.printf("status: %d\n", sensorValue.status);
    // Serial.printf("ypr: %f %f %f\n", ypr.yaw, ypr.pitch, ypr.roll);
    Serial.printf("voltage: %f\n", battery_filt);
    Serial.printf("mot_angle: %f\n", mot_angle * RAD_TO_DEG);
    // Serial.printf("mot_angle_zeroed: %f\n", (mot_angle+motor_zero) * RAD_TO_DEG);
    Serial.printf("u: %f %f %f\n", u[0], u[1], u[2]);
    Serial.printf("v: %f %f %f\n", v[0], v[1], v[2]);
    // Serial.printf("w: %f %f %f\n", w[0], w[1], w[2]);
    // Serial.printf("proj: %f\n", proj_angle * RAD_TO_DEG);
    Serial.printf("d: %f %f\n", d[0], d[1]);
    // Serial.printf("outint: %d\n", output_int);
    Serial.printf("vel_des: %f\n", vel_volt_ctrl_filt);


    Serial.printf("thetaM: %f\n", thetaM * RAD_TO_DEG);
    Serial.printf("thetaMtoMotor: %f\n", thetaM_motor * RAD_TO_DEG);

    Serial.printf("telemetry: %s\n", payload);


    static long time_print = 0;

    // Serial.printf("time_mot_read: %d\n", time_mot_read);
    // Serial.printf("time_imu_read: %d\n", time_imu_read);
    // Serial.printf("time_nn: %d\n", time_nn);
    // Serial.printf("time_mot_set: %d\n", time_mot_set);
    // Serial.printf("time_espnow: %d\n", time_espnow);
    // Serial.printf("time_print: %d\n", time_print);
    Serial.printf("total: %d\n", time_mot_read+time_imu_read+time_nn+time_mot_set+time_espnow+time_print);
    // Serial.printf("kp: %f\n", kp);
    // Serial.printf("kd: %f\n", kd);
    time_print = micros() - last;
    last = micros();

    // Serial.printf("oint: %d\n", output_int);

    // for (int i = 0; i < INPUT_SIZE; i++){
    //     // Serial.printf("%f ", obs[i]);
    //     Serial.printf("%d ", input->data.int8[i]);
    // }
    // Serial.printf("\n");



    // Serial.printf("cmdx: %d\n", cmdx);
    // Serial.printf("temp: %f\n", coil_temp);
    // Serial.printf("cmdy: %d\n", cmdy);
    // Serial.printf("run0: %d\n", run0);
    // Serial.printf("output: %f\n", output_float);
    Serial.printf("\t\n");

    // delay(5);
}

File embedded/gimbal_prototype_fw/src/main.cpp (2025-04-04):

#include <Arduino.h>
#include <Adafruit_BNO08x.h>
#include <iq_module_communication.hpp>
#include <esp_now.h>
#include <WiFi.h>

IqSerial ser(Serial1);
PowerMonitorClient power(0);
MultiTurnAngleControlClient angle(0);

uint8_t estop_mac_addr[] = {0x30, 0x30, 0xF9, 0x34, 0x52, 0xA0};


String receivedString = "";
char send_str[255];

void OnDataRecv(const uint8_t *mac, const uint8_t *incomingData, int len) { // len should not be longer than 250bytes
    receivedString = String((char *)incomingData);
}

void OnDataSent(const uint8_t *mac_addr, esp_now_send_status_t status) {

}




void setup() {
    // Initialize the IqSerial object
    // ser.begin();
    setCpuFrequencyMhz(80);


    // Serial1.begin(115200, SERIAL_8N1, D1, D0);
    Serial1.begin(115200, SERIAL_8N1);
    pinMode(LED_BUILTIN, OUTPUT);
    pinMode(D2, OUTPUT);
    digitalWrite(D2, LOW); // ground reference for IQ motor

    
    Serial.begin(115200);
    delay(1000);

    // ESP NOW SETUP
    WiFi.mode(WIFI_MODE_STA);
    Serial.println(WiFi.macAddress());
    if (esp_now_init() != ESP_OK) {
        Serial.println("Error initializing ESP-NOW");
        delay(3000);
        ESP.restart();
    }
    esp_now_register_recv_cb(OnDataRecv);
    esp_now_register_send_cb(OnDataSent);
    esp_now_peer_info_t peerInfo = {};
    memcpy(peerInfo.peer_addr, estop_mac_addr, 6);
    peerInfo.channel = 0;
    peerInfo.encrypt = false;
    esp_now_add_peer(&peerInfo);
}

// int f0 = 4096; //ranges from 0 to 8192, 4096 is center
// int m0 = 0; // 0: voltage control, 1: angle control

int cmdx = 0;
int cmdy = 0;
int run0 = 0;
long dt = 0;


void loop() {


    float battery_voltage = 0;
    ser.get(power.volts_, battery_voltage);
    
    // if (m0 == 0) {
    //     // voltage control
    //     float ctrl_voltage = (f0 - 4096) / 4096.0f * 7.4f;
    //     ser.set(angle.ctrl_volts_, ctrl_voltage);
    // }else{
    //     // angle control
    //     float angle_deg = (f0 - 4096) / 4096.0f * 2*PI;
    //     ser.set(angle.ctrl_angle_, angle_deg);
    // }

    // // ESP NOW receive and send
    // if (receivedString.indexOf("f0") != -1) { // data exists
    //     f0 = receivedString.substring(receivedString.indexOf("f0") + 3, receivedString.indexOf("f0") + 8).toInt();
    //     m0 = receivedString.substring(receivedString.indexOf("m0") + 3, receivedString.indexOf("m0") + 8).toInt();
    // }

    
    // size_t send_str_size = sprintf(send_str,
    //     "v:%.2f\n"
    //     ,
    //     battery_voltage
    // );
    // esp_now_send(estop_mac_addr, (uint8_t *) send_str, send_str_size);


    // ESP NOW receive and send
    if (receivedString.indexOf("cmdx") != -1) { // data exists
        cmdx = receivedString.substring(receivedString.indexOf("cmdx") + 5, receivedString.indexOf("cmdx") + 10).toInt();
        cmdy = receivedString.substring(receivedString.indexOf("cmdy") + 5, receivedString.indexOf("cmdy") + 10).toInt();
        run0 = receivedString.substring(receivedString.indexOf("run0") + 5, receivedString.indexOf("run0") + 10).toInt();
    }
    size_t send_str_size = sprintf(send_str,
        "v:%.2f\n"
        ,
        battery_voltage
    );
    esp_now_send(estop_mac_addr, (uint8_t *) send_str, send_str_size);

    // Serial.printf("v:%.2f\n", battery_voltage);
    // // Serial.printf("f0:%d m0:%d\n", f0, m0);

    Serial.printf("dt: %d\n", dt);
    // Serial.printf("status: %d\n", sensorValue.status);
    // Serial.printf("yaw: %f\n", ypr.yaw);
    // Serial.printf("pitch: %f\n", ypr.pitch);
    // Serial.printf("roll: %f\n", ypr.roll);
    Serial.printf("voltage: %f\n", battery_voltage);
    Serial.printf("cmdx: %d\n", cmdx);
    Serial.printf("cmdy: %d\n", cmdy);
    Serial.printf("run0: %d\n", run0);
    Serial.printf("\t\n");

    delay(1);
}

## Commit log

2025-02-07 add option for position control, but switching from volt to pos control goes crazy
2025-02-11 get urdf of parametric 1dof rock
    [Part_2_1.stl, Part_3_1.stl, Part_4_1.stl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]
2025-02-11 remove onshape_dir prepath bc already enforced
    [Part_2_1.stl, Part_3_1.stl, Part_4_1.stl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]
2025-02-15 simulate basic rock
    [Part_2_1.stl, Part_3_1.stl, Part_4_1.stl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]
2025-02-19 set up onshape urdf pipeline, training except for torques,obs
    [foot_1.stl, pendulum_1.stl, pmrock.urdf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]
2025-02-20 a bunch of training, parameter tuning
    [foot_1.stl, pendulum_1.stl, pmrock.urdf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]
2025-02-25 balo sim
    [balo.urdf, bottomshell_1.stl, pendulum_1.stl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]
2025-02-26 figure out how to set initial dof and base vels
    [balo.urdf, balo_penroot.urdf, bottomshell_1.stl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]
2025-03-11 try casadi trajopt, create balo2 from onshape
    [balo_2.urdf, pendulum_1.stl, shell1_1.stl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]
2025-03-11 generate traj for t=6, delete some empty tumble trainings
    [balo_2.urdf]
2025-03-12 make new reward function nonzero, trains kinda
    [balo.urdf, balo_2.urdf]
2025-03-14 realistic rock neural net (in:42 [128,128,128] out:1) runs on esp32 at 640Hz
2025-03-15 restructure, add little documentation to embedded
    [balo.urdf, balo_2.urdf]
2025-03-17 cmd tracking train attempts
    [Part_1_1.stl, Part_1_2.stl, balo.urdf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]
2025-03-17 cmdtumble_2025-03-17_00-03-51 trained smoothly, value loss keeps increasing tho
    [balo.urdf]
2025-03-17 faster rolling with jack's hellorock cad
    [balo.urdf, hellorock.urdf]
2025-03-17 velocity misalignment penalty helps
    [hellorock.urdf]
2025-03-18 added hellorock w battery and motor, hyperparameter sweep
    [IQ2306_Simplified_1.stl, hellorock_elec.urdf, leadestimation_1.stl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]
2025-03-18 hyperparameter sweep of gamma, lam, numstepsperenv
    [hellorock_elec.urdf]
2025-03-26 train successful intuition2 shell
    [2x3_battery_pack_1_SUB_tattu_220mah_battery_1.stl, 2x3_battery_pack_1_SUB_tattu_220mah_battery_2.stl, 2x3_battery_pack_1_SUB_tattu_220mah_battery_3.stl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]
2025-03-26 figure out how to set dof armature for more realistic torque values
2025-03-27 torque limit and domain randomization w fric, mass shift, com shift
    [intuition2.urdf]
2025-03-27 train with better resampling time, seed, misalignment penalty on sim desktop
    [eval_ckpt-1.csv, eval_ckpt1250.csv, eval_ckpt2150.csv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]
2025-03-28 train with action rate penalty, 14-44-41 model_1350 looks good
    [eval_ckpt1350.csv, intuition2.urdf]
2025-03-28 rock2_fw vel control
    [2025-03-27_14-44-41_1350.csv]
2025-04-03 create folder in sandbox to test linear velocity est from imu
2025-04-03 shaky results for integrating imu acceleration for linear velocity
    [eval_ckpt1350.csv, eval_ckpt2150(2).csv]
2025-04-03 low pass filter doesn't help, only slightly better than like predicting zeros
2025-04-11 train trying to lower action rate
    [eval_ckpt1000(2).csv, eval_ckpt400(2).csv, eval_ckpt500.csv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]
2025-04-11 make 56-38 model available, trained for 16V max
2025-04-11 convert model to tflite, not hardware tested
    [2025-04-11_12-56-38_500.csv]
2025-04-13 find that obs quantization scale was calculated wrong
    [main.cpp, rockstation2.py]
2025-04-13 train and eval 55-41 for [-1,1] obs range
    [2025-04-12_22-10-04_500.csv, 2025-04-12_22-55-41_1000.csv, eval_ckpt1000.csv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]
2025-04-13 find that angular vel obs need to be in local not global frame
2025-04-13 added quaternion multiplier for quaternion transformation to global frame
2025-04-14 train with quat and angvel in base frame (urdf)
    [2025-04-13_17-17-11_450.csv, eval_ckpt100.csv, eval_ckpt450.csv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]
2025-04-15 speed up looptime to 88Hz, update quat transform
2025-04-15 train a lot more vel control and penalty on dof rate
    [eval_ckpt100.csv, eval_ckpt150.csv, eval_ckpt200.csv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]
2025-04-15 train 58-02 on dt0.012, smoother
    [eval_ckpt1000_s1.csv, eval_ckpt200.csv, eval_ckpt200_s1.csv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]
2025-04-15 prepare firmware for velocity nn
    [2025-04-15_01-58-02_200.csv]
2025-04-15 transfer model from trained on terrain 13_26_700
    [2025-04-15_10-13-26_700.csv, eval_ckpt1000_s1.csv, eval_ckpt150_s1.csv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]
2025-04-15 try manual velocity control on esp instead of vertiq
2025-04-15 final 35-30 training
    [intuition2.urdf]
2025-04-16 analyze successful rect trajectory, workshop abstract submitted!
    [rocktrack.csv]
2025-04-26 added csv file writer
    [intuition2.urdf]
2025-04-26 working csv writer
    [output_2025-04-26_1609.csv]
2025-04-27 using crank to control pendulum angle
    [output_2025-04-26_1611.csv, output_2025-04-26_1612.csv, output_2025-04-26_1614.csv]
2025-05-04 encoding and decoding in base64 for rock telemetry, log telemetry, organized rockstation2
    [2025-05-03_2203.csv]
2025-06-21 more info in readme
    [output_2025-04-26_1609.csv, output_2025-05-21_0015.csv]
